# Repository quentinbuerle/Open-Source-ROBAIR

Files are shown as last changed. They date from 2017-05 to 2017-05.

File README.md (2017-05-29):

# Open-Source-ROBAIR

A new open source version of the ROBAIR project originally designed by Jérôme Maisonnasse

 Welcome to the RobAir Open source project!
 ====================

If you read this, then you probably show some interest in our project Robair. In this guide, we are going to show you the method we used to build our very own Robair. This project is still a prototype, so obviously the method we chose is not perfect and can be improved. Feel free to do your own changes and share with us your upgrades! Just keep in mind that the following guide is just an example of how you can build Robair, and you can change it if you have a better way of doing it.
 
Required material : Plexiglas, PVC tube.
Required components: Hoverboard, battery charger, pole, idler wheel (x2), nuts, screws, washers.
Required machines : Laser cutting machine using CorelDraw,  3D Printer using Repetier Host, Stratoconception using StratoConcept, saw, folding machine, rulers, screwdriver, files.
 
I- How to build a Robair similar to our :
 ====================

Step 1: Machining of the pieces thanks to the laser cutting machine 
---------
       
  Get the .dxf files provided on Github [DFX FILES](https://github.com/cinatalia/Open-Source-ROBAIR/tree/master/DFX)
      
  Open CorelDraw
      
  Import the files that you wish to cut (be careful to the dimensions of the plate and the thickness of the parts).
      
  Choose the option “very fine outlines” and “connect the curvatures”.
      
  Print the file after selecting the adapted parameters for the plate thickness.
       
  Place the plate on the correct position and initialize the origin.
      
  Activate the ventilation.
      
  Launch the program.
 
Step 2: Machining of the pieces thanks to the 3D Printer:
---------
      
  Get the .stl files provided on Github [STL FILES](https://github.com/cinatalia/Open-Source-ROBAIR/tree/master/STL)
  
  Open Repetier Host.          
 
Step 3 : Machining of the pieces thanks to StratoConception : 
---------
       
  Get the .stl files provided on GitHub [STL FILES](https://github.com/cinatalia/Open-Source-ROBAIR/tree/master/STL)
  
  Open StratoPro.
 
  Choose the correct thickness and positioning of the slices according to the thickness of the available plates.
 
  Define the positioning of the inserts (metal rods used to maintain the alignment when we glue the differents slices together.
  
  Choose the correct tool for the cutting.
  
  Check that the tool path matches the geometry of the parts.
 
  Create the machine code and put it into the tower. 

Step 4: Folding the pieces : 
---------
As you may have noticed, some pieces have been folded to simplify the building of our Robair. 

To fold the pieces, start by cutting the pattern file with the laser cutting machine. Then, simply draw a line where you went to bend the part and using the folding machine, heat the line until it’s limp enough to be folded at the correct angle.

Step 5 : Assembly and mounting of Robair :
---------

   Now that you have all the components of Robair, you can start the assembly.

 II- How to build a different Robair : 
  ====================

In case you want to change the structure of the robot and add your own upgrades, you only have to follow these steps :

Get the CAD files provided on GitHub. The files are available in different formats; [.PRT](https://github.com/cinatalia/Open-Source-ROBAIR/tree/master/Original%20version%20Creo%20.PRT), [.STEP](https://github.com/cinatalia/Open-Source-ROBAIR/tree/master/STEP), [.IGES](https://github.com/cinatalia/Open-Source-ROBAIR/tree/master/IGES)

If you use Creo, SolidWorks or Catia, the .prt and .step files will do just fine. However, if you want to use a free open source CAD software like FreeCAD, know that the .iges format is pretty standard and should work on any software you use
change the design of the CAD  go back to part I and follow the steps. 

Enjoy it...
---------

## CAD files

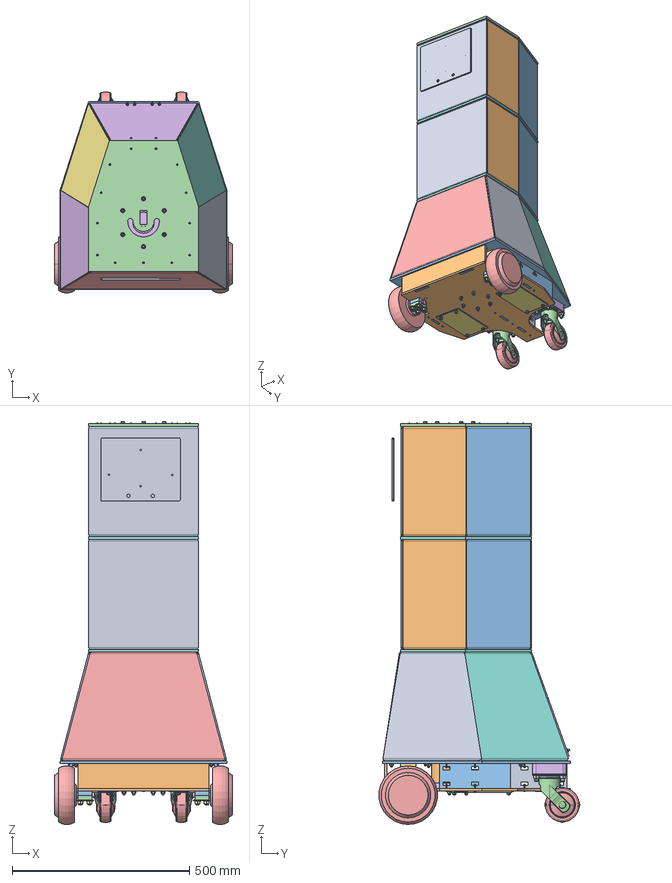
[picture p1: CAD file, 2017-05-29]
STEP/robair_complete_assembly_asm.stp
502.0 x 566.5 x 1136.0 mm
BE1
SR1 x 2
SR2 x 2
R x 2
SM1
SR3 x 4
SP1
CE
M
BE2
RF_A x 2
RF_B x 2
AD1 x 2
SB x 2
BATTERIE x 2
S1
S3
S2 x 2
SM2 x 4
V_A x 4
PIN x 2
ISO4762-M10X60-8_8 x 8
DINENISO7090-10 x 16
ISO4032-M10-6 x 8
ISO4762-M6X35-10_9 x 30
DINENISO7090-6 x 90
ISO4032-M6-6 x 47
DIN7984-M3X20-8_8 x 25
DINENISO7092-3 x 32
ISO4032-M3-6 x 29
ISO4014-M3X20-5_6 x 2
DINENISO7092-6 x 2
ISO2009-M4X20-4_8 x 8
ISO4032-M4-6 x 8
ISO4762-M6X20-10_9 x 8
VR x 8
WA38 x 16
RHN38 x 16
BE3 x 2
CS1
CS2 x 4
CS3 x 2
CT1
BE4
CP1
CP2
CP3
CP5
CP6
SV x 2
ISHCS0408 x 29
IWPNA04 x 27
INHS104 x 27
CP4
DINENISO7092-4 x 4
ISO4762-M6X22-10_9 x 7
H

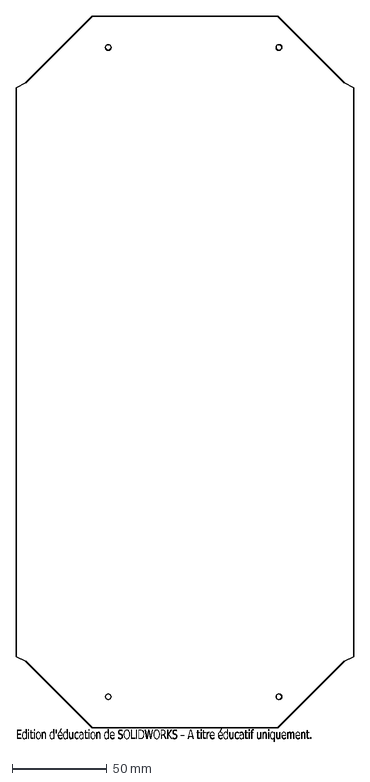
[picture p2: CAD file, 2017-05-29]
DFX/cs2.DXF
Edition d'éducation de SOLIDWORKS – A titre éducatif uniquement.

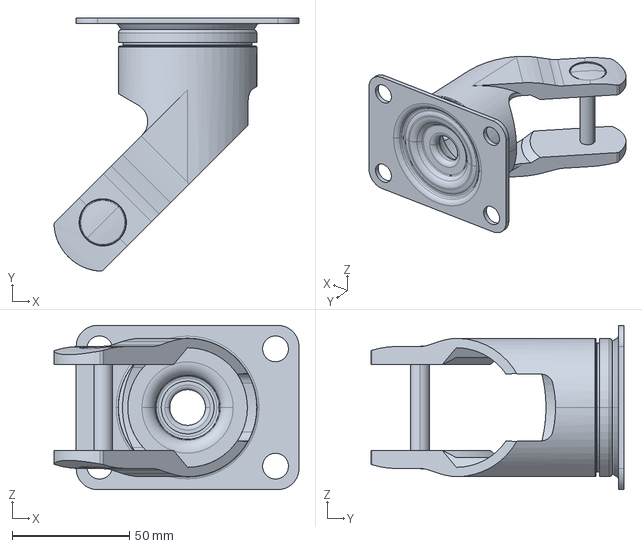
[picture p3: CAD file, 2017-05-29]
STEP/rf_a.stp
104.5 x 108.0 x 70.0 mm

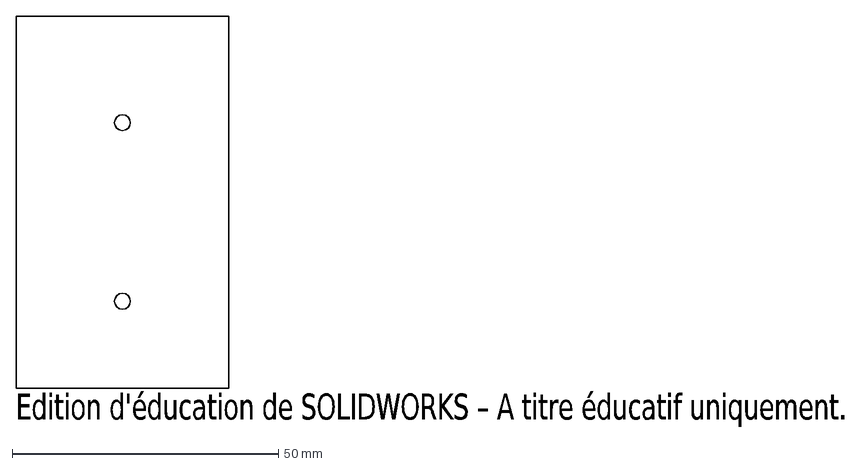
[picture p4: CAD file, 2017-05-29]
DFX/sv.DXF
Edition d'éducation de SOLIDWORKS – A titre éducatif uniquement.

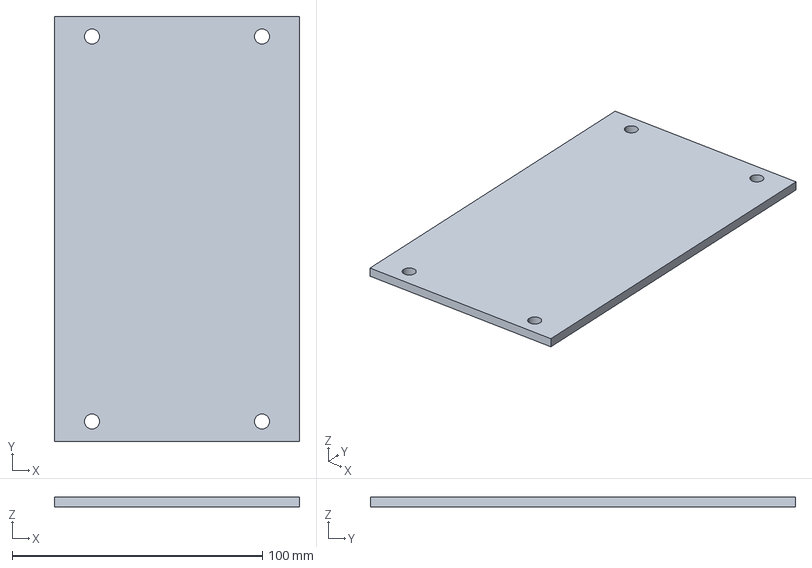
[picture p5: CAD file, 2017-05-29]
STEP/sb.stp
98.0 x 170.0 x 4.00 mm

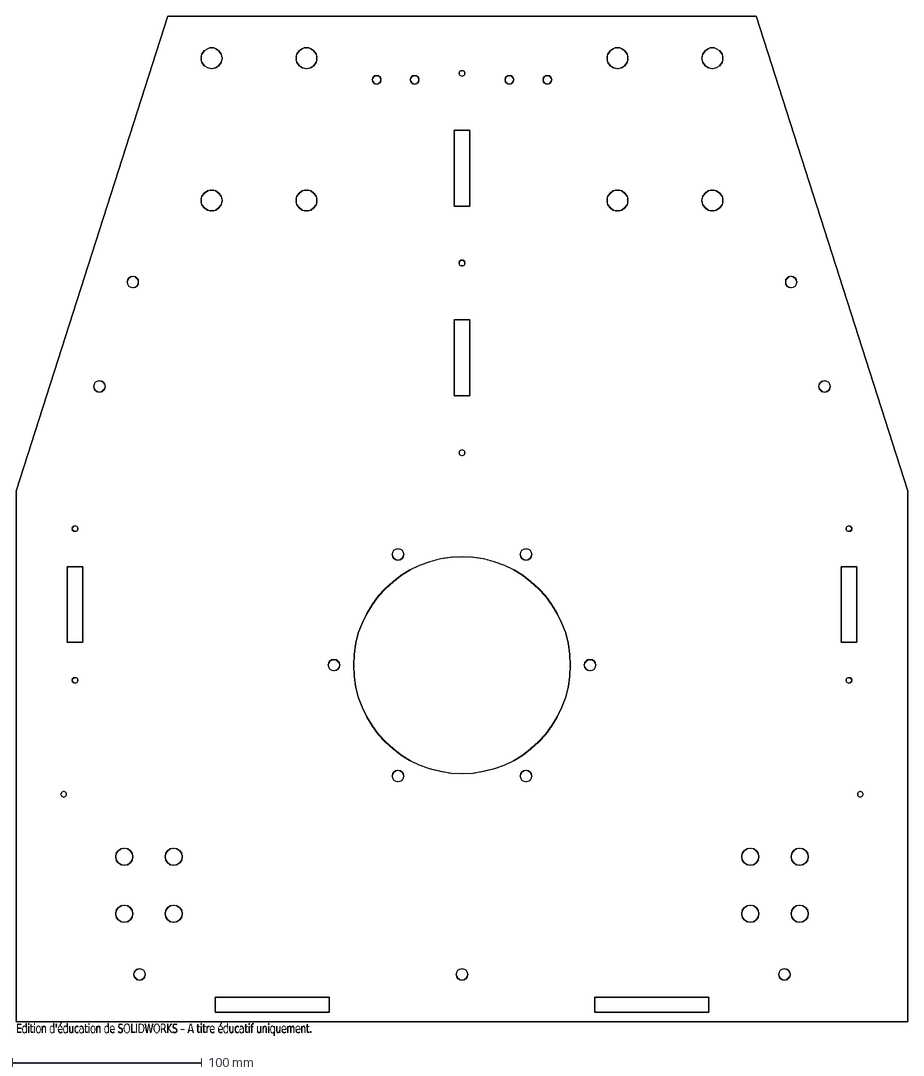
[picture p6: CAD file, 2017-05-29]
DFX/be2.DXF
Edition d'éducation de SOLIDWORKS – A titre éducatif uniquement.

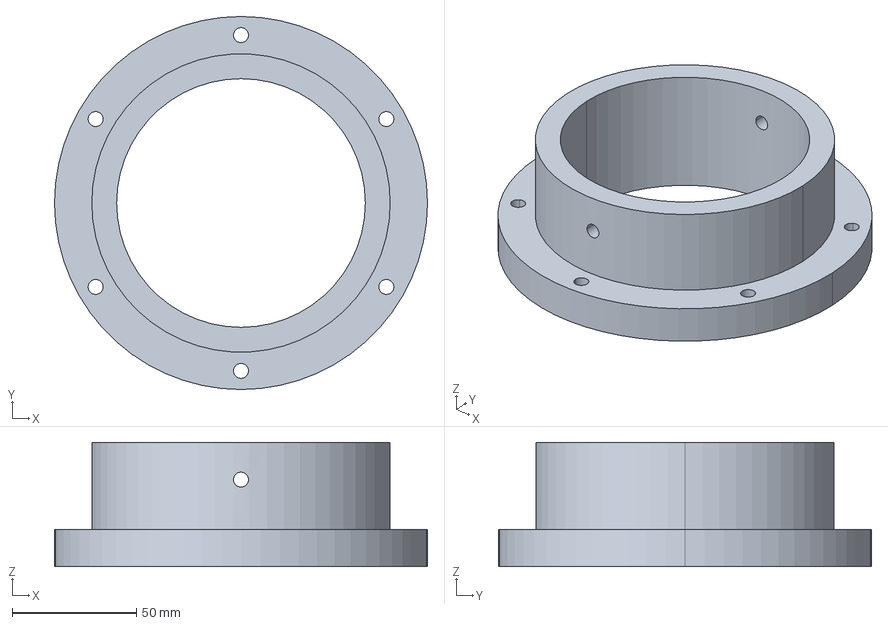
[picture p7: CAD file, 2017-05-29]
STEP/sm2.stp
150.0 x 150.0 x 50.0 mm

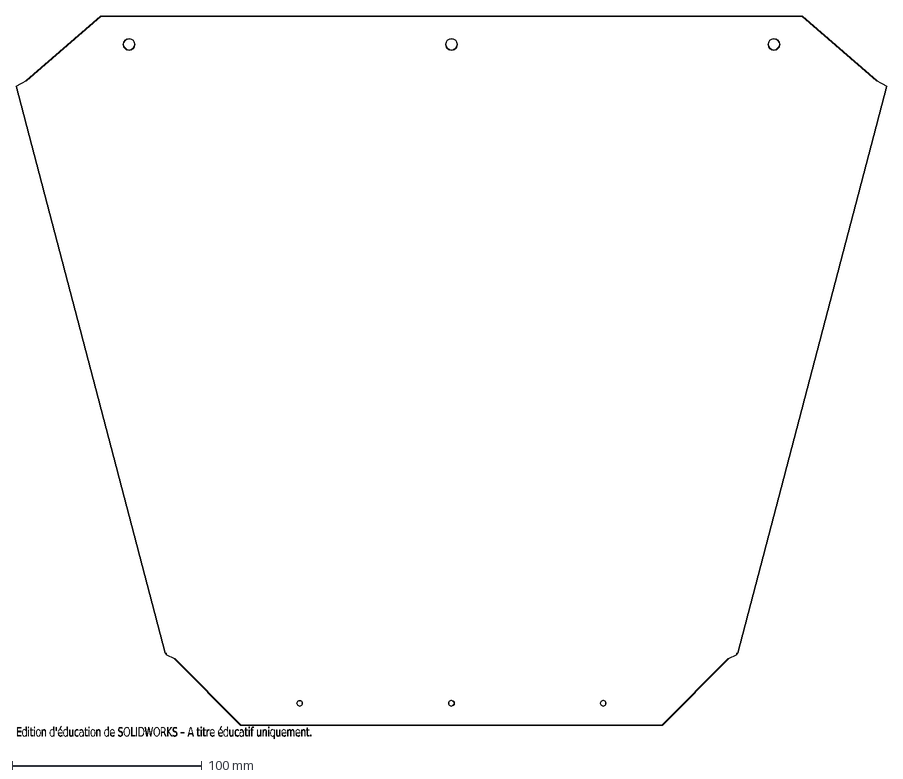
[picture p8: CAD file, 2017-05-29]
DFX/cp1.DXF
Edition d'éducation de SOLIDWORKS – A titre éducatif uniquement.

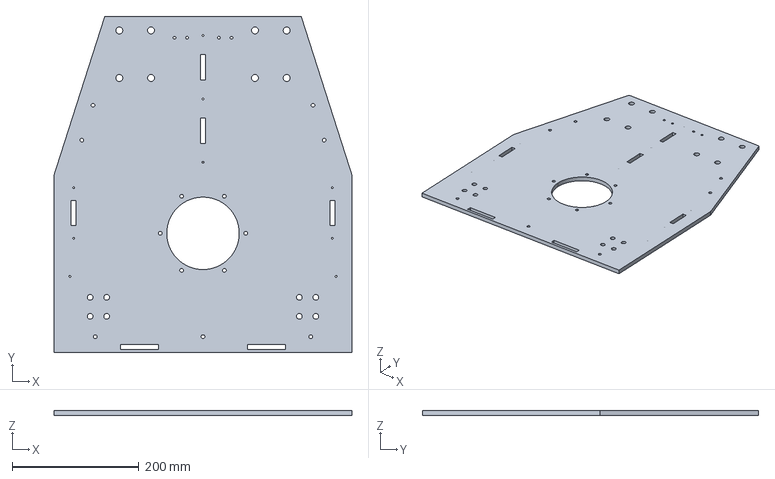
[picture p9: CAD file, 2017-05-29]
STEP/be2.stp
470.0 x 530.0 x 8.00 mm

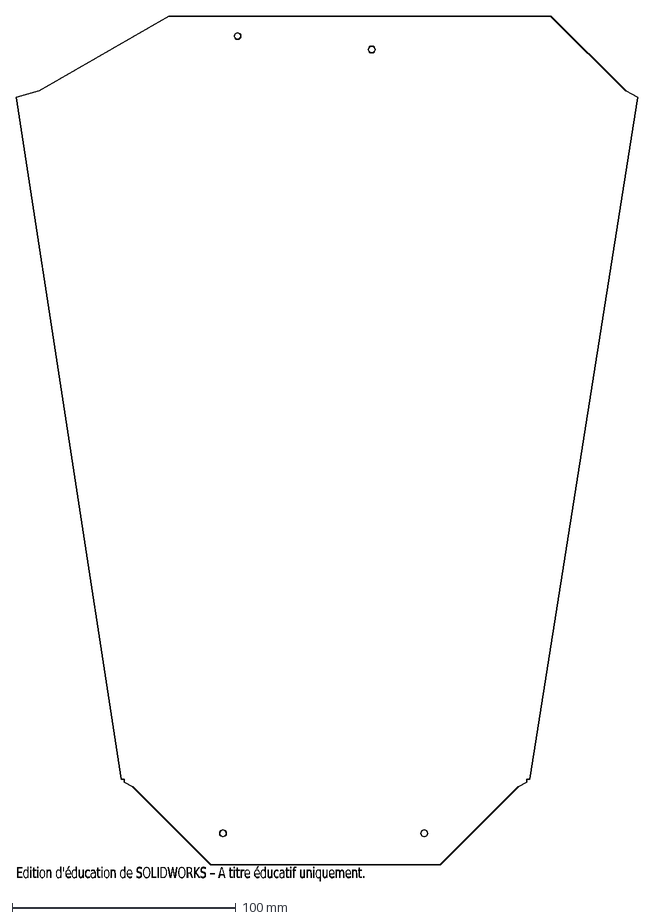
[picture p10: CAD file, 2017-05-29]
DFX/cp6.DXF
Edition d'éducation de SOLIDWORKS – A titre éducatif uniquement.

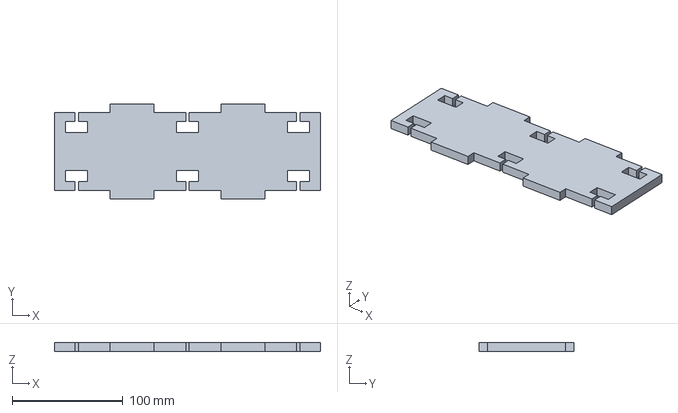
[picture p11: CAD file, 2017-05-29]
STEP/s1.stp
240.0 x 86.0 x 8.00 mm

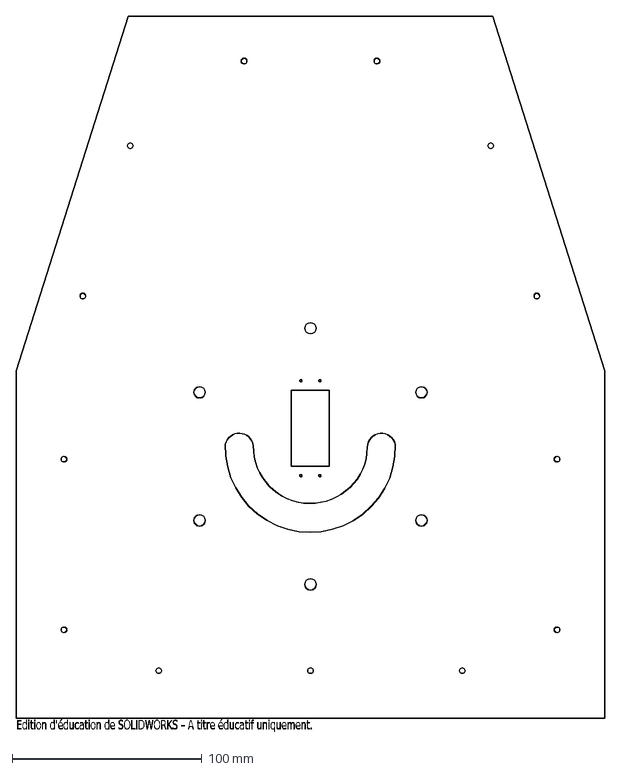
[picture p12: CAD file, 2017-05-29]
DFX/be4.DXF
Edition d'éducation de SOLIDWORKS – A titre éducatif uniquement.

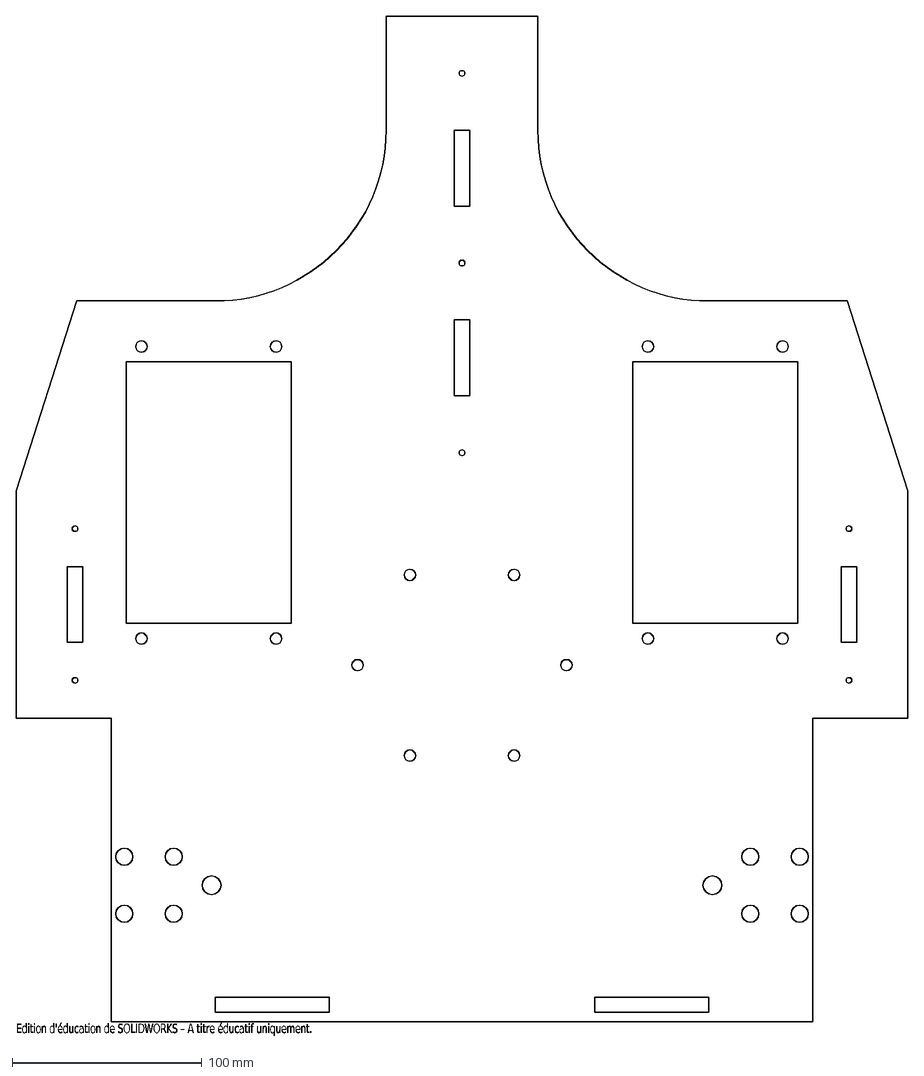
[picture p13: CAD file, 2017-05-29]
DFX/be1.DXF
Edition d'éducation de SOLIDWORKS – A titre éducatif uniquement.

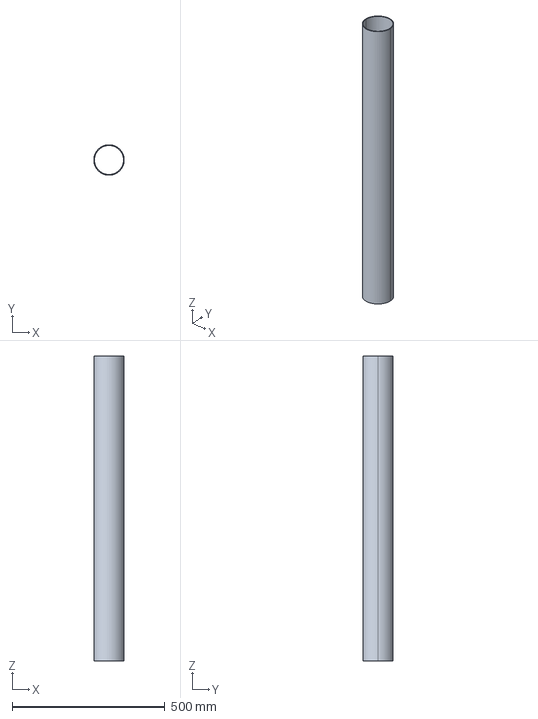
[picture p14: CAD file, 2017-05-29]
STEP/m.stp
100.0 x 100.0 x 1000.0 mm

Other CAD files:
DFX/cp3.DXF
STEP/s2.stp
DFX/cp4.DXF
STEP/be1.stp
DFX/be3.DXF
DFX/cp2.DXF
DFX/cp5.DXF
DFX/cs1.DXF
DFX/cs3.DXF
DFX/ct1.DXF
DFX/h.DXF
DFX/s1.DXF
DFX/s2.DXF
DFX/s3.DXF
DFX/sb.DXF
IGES/ad1.igs
IGES/be1.igs
IGES/be2.igs
IGES/be3.igs
IGES/be4.igs
IGES/cp1.igs
IGES/cp2.igs
IGES/cp3.igs
IGES/cp4.igs
IGES/cp5.igs
IGES/cp6.igs
IGES/cs1.igs
IGES/cs2.igs
IGES/cs3.igs
IGES/ct1.igs
IGES/h.igs
IGES/m.igs
IGES/r.igs
IGES/rf_a.igs
IGES/s1.igs
IGES/s2.igs
IGES/s3.igs
IGES/sb.igs
IGES/sm1.igs
IGES/sm2.igs
IGES/sp1.igs
IGES/sr1.igs
IGES/sr2.igs
IGES/sr3.igs
IGES/sv.igs
IGES/v_a.igs
STEP/ad1.stp
STEP/be3.stp
STEP/be4.stp
STEP/cp1.stp
STEP/cp2.stp
STEP/cp3.stp
STEP/cp4.stp
STEP/cp5.stp
STEP/cp6.stp
STEP/cs1.stp
STEP/cs2.stp
STEP/cs3.stp
STEP/ct1.stp
STEP/h.stp
STEP/r.stp
STEP/s3.stp
STEP/sm1.stp
STEP/sp1.stp
STEP/sr1.stp
STEP/sr2.stp
STEP/sr3.stp
STEP/sv.stp
STEP/v_a.stp
STL/ad1.stl
STL/sm1.stl
STL/sm2.stl
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

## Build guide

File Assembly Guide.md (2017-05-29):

# Assembly guide

## Step 1: Assembly the RobAir Base

Code Name | Description | Quantity | Manufacturing Method | Files 
------------ | ------------- | ------------- | ------------- | ------------- 
BE1| Main Base | 1 | Laser Cutting  |	[BE1](https://github.com/cinatalia/Open-Source-ROBAIR/blob/master/DFX/be1.DXF)	
BE2 | 	Second Base| 	1	| Laser Cutting| [BE2](https://github.com/cinatalia/Open-Source-ROBAIR/blob/master/DFX/be2.DXF)
SR1	| Wheel carrier 1| 	2| 	Stratoconception| [SR1](https://github.com/cinatalia/Open-Source-ROBAIR/blob/master/STL/sr1.stl)
SR2| 	Wheel carrier 2| 	2	| Stratoconception| [SR2](https://github.com/cinatalia/Open-Source-ROBAIR/blob/master/STL/sr2.stl)
SR3| 	Wheel carrier 3| 	2	| Stratoconception| [SR3](https://github.com/cinatalia/Open-Source-ROBAIR/blob/master/STL/sr3.STL)
AD1	| Caster wheel adapter| 	2	|Stratoconception|[AD1](https://github.com/cinatalia/Open-Source-ROBAIR/blob/master/STL/ad1.stl)
SB| 	Battery carrier| 	2	| Laser Cutting| [SB](https://github.com/cinatalia/Open-Source-ROBAIR/blob/master/DFX/sb.DXF)
SP1| 	Electronical board carrier| 	1	| Laser Cutting| [SP1](https://github.com/cinatalia/Open-Source-ROBAIR/blob/master/DFX/sp1.DXF)
S1| 	Middle Divider plate|  	1	| Laser Cutting| [S1](https://github.com/cinatalia/Open-Source-ROBAIR/blob/master/DFX/s1.DXF)
S2| 	Side Divider Plate| 	2| 	Laser Cutting| [S2](https://github.com/cinatalia/Open-Source-ROBAIR/blob/master/DFX/s2.DXF)
S3| 	Back Divider Plate| 	1| 	Laser Cutting| [S3](https://github.com/cinatalia/Open-Source-ROBAIR/blob/master/DFX/s3.DXF)
SM1| 	Mast support main base| 	1| 	Stratoconception| [SM1](https://github.com/cinatalia/Open-Source-ROBAIR/blob/master/STL/sm1.stl)
V_A| 	Hinge| 	4	| 3D printing| [V_A](https://github.com/cinatalia/Open-Source-ROBAIR/blob/master/STL/v_a.stl)
M| 	Mast| 	1	| Cut a PVC tube (1m)| 

### Base assemmbling:
Upper view assembling |Bottom view assembling
------------ | ------------- 
 | 

### Complete base assembling:

<p align="center"> 

</p>

## Step 2: Assembly the RobAir Body

Code Name | Description | Quantity | Manufacturing Method | Files 
------------ | ------------- | ------------- | ------------- | ------------- 
BE3|	Third Base	|1	|Laser Cutting|[BE3](https://github.com/cinatalia/Open-Source-ROBAIR/blob/master/DFX/be3.DXF)	
BE4|	Fourth Base|	1	|Laser Cutting|[BE4](https://github.com/cinatalia/Open-Source-ROBAIR/blob/master/DFX/be4.DXF)	
SM2|	Mast support	|3|	Stratoconception|[SM2](https://github.com/cinatalia/Open-Source-ROBAIR/blob/master/STL/sm2.stl)
CS1|	Front panel 2|	1	|Laser Cutting|[CS1](https://github.com/cinatalia/Open-Source-ROBAIR/blob/master/DFX/cs1.DXF)	
CS2|	Lateral panel|	4	|Laser Cutting|[CS2](https://github.com/cinatalia/Open-Source-ROBAIR/blob/master/DFX/cs2.DXF)	
CS3	|Back Panel 3|	1|	Laser Cutting|[CS3](https://github.com/cinatalia/Open-Source-ROBAIR/blob/master/DFX/cs3.DXF)	
CT1	|Front panel 3|	1	|Laser Cutting|[CT1](https://github.com/cinatalia/Open-Source-ROBAIR/blob/master/DFX/ct1.DXF)	
CP1|	Front panel 1|	1|	Laser Cutting|[CP1](https://github.com/cinatalia/Open-Source-ROBAIR/blob/master/DFX/cp1.DXF)	
CP2|	Left-hand side panel 1|	1	|Laser Cutting|[CP2](https://github.com/cinatalia/Open-Source-ROBAIR/blob/master/DFX/cp2.DXF)	
CP3|	Left-hand rear panel 1|	1	|Laser Cutting|[CP3](https://github.com/cinatalia/Open-Source-ROBAIR/blob/master/DFX/cp3.DXF)	
CP4	|Rear Panel 1|	1|	Laser Cutting|[CP4](https://github.com/cinatalia/Open-Source-ROBAIR/blob/master/DFX/cp4.DXF)	
CP5|	Right-hand rear panel 1|	1|	Laser Cutting|[CP5](https://github.com/cinatalia/Open-Source-ROBAIR/blob/master/DFX/cp5.DXF)	
CP6|	Right-hand side panel 1|	1|	Laser Cutting|[CP6](https://github.com/cinatalia/Open-Source-ROBAIR/blob/master/DFX/cp6.DXF)	
SV|	Bracket Rear panel	|2|	Laser Cutting|[SV](https://github.com/cinatalia/Open-Source-ROBAIR/blob/master/DFX/sv.DXF)	
H	|Tablet Holder	|1	|Laser Cutting|[H](https://github.com/cinatalia/Open-Source-ROBAIR/blob/master/DFX/h.DXF)	

### First Module Body:
Front Parts | Back Parts
------------ | ------------- 
firstmodulebody | 

### Second and Third Module Body:
Front Parts | Back Parts
------------ | ------------- 
 | 

### Complete assembling:


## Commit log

2017-05-22 Parts in STEP format
    Here you can find all the CAD files of RobAir in STEP format
    [ad1.stp, be1.stp, be2.stp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]
2017-05-22 Parts in IGES Format
    Here you can find all the CAD files of RobAir in IGES format
    [ad1.igs, be1.igs, be2.igs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]
2017-05-22 Files DFX Laser Cutting
    Here you find the files .DFX ready to be use in the laser machine
    [be1.DXF, be2.DXF, be3.DXF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]
2017-05-22 Files DFX Laser Cutting
    [sv.DXF]
2017-05-22 Files in STL format
    [ad1.stl, sm1.stl, sm2.stl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]
2017-05-23 Create Assembly Guide
2017-05-23 Update Assembly Guide
2017-05-23 Rename Assembly Guide to Assembly Guide.md
2017-05-23 Update Assembly Guide.md
